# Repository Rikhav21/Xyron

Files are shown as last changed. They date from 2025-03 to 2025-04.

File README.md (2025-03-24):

# The 3d printer
This is just my CoreXY 3d printer that I want to print the frame for, and am trying to make the printer as cheap as possible.
The printer should end up being less than 150 dollars, but I also hope to make a filament extrusion system, and it also function as a laser cutter if needed. 
## CAD
This is the link for Onshape cad. https://cad.onshape.com/documents/d1304014e73009d6c11ef726/w/34172c7cf5d371a968e193e7/e/cf54ac2cfe94093a287dfb58
The CAD for this is in a step file, but does not have the belts, but they should go around the stepper botors, and attatach to the print head though the holes.

Design
## BOM
I tried to make it less than 150 dollars. http://docs.google.com/spreadsheets/d/1EGhT13h8WIjT6__bsCRffLh4skm1RX1gYrO3IXuM8uQ/edit?gid=0#gid=0

BOM

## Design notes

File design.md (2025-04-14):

made by @Rmardia \
Repositiory link: https://github.com/Rikhav21/Xyron \
Total hours so far: 74.5
- [x] I have a 3d printer right now.
## Day one
### Research
Today I spent a lot of time looking an=t a lot of different options and at the end I decided on making a core XY machine. I looked through a lot of different models on printables and I think I got the basic principles of how one of these machines would work.
### My goal
My goal with this 3d printer is to 3d print as many of the parts as possible from the frame, to whatever crosses my mind. I also feel like a auto print remover would be something simple to add with just a servo, that would make the printer way cooler.
### Design
I started with onshape, and got a liitle of the gantry done. 
### time
4 hours 30 minutes

IMounting 
## Day two
### Design
Today I learnt a little bit more about onShape and got continued with the assembaly. Most of my time just was spent figuring out how to use the assembaly.
### Time
5 hours and 30 minutes

gantry
## Day three
### Design
Today I continues working on the gantry and now have to work on the tool head. The X and Y linear rods are finished with the modeling.
### Time
6 hours.

gantry
## Day four
### Design
Today I did a lot of work on the gantry, and added some screws on the assembally, however I realized that I forgot about the idelers, so I have to do that later. 
### Time
Today I spent 5 hours on the design.
## Day five
### Design
Today I have redesign a lot of the parts because I forgot the idlers, I also redid the assembally and a ton of the parts, It was so annoying that I had to make so many changes for one tiny thing
Time 5 and a half hours.
## Day six
### Design
Today I did a lot of designing, made the x axis with the linear rods, and though about ways that I could do bed leveling. I decided on just using screws, and rubber bands to hold the bed in place
### Time
Six and a half hours.
## Day seven
### Design
Today I continued working on the bed and started my BOM.BOM. I finished most of it, then realized that I would also need am extruder, so I had to model a mount for that.
### Time
8 hours.
BOM
## Day Eight
### Design
Today I worked on the z axis movement and got some suggestions for the printer, so I also added some clearances. I updated my BOM, and got it down to $130 (Not counting filament, or taxes), and I realized that I forgot to mount my SKR Mini, so I will do that tomorrow.
https://docs.google.com/spreadsheets/d/1EGhT13h8WIjT6__bsCRffLh4skm1RX1gYrO3IXuM8uQ/edit?usp=drivesdk

### TIme
4 and a half hours.
## Day nine
### Design
Today I just adjusted some clearances, and mounted the board to the printer. I guess that Now I will submit the file, and ask for the grant, so I will keep my fingers crossed that it will get accepted.
Design
### Time
2 hours.

## Day nine
### Design
Today I mainly just ordered parts, and researched for some better deals. I also researched for a filament extruder.
### Time
Five and a half hours.

## Day ten
### Design
Today I satrted getting some of parts, and just did some assembling, and printed a hot end holder out of petg, although I did suffer some stringing, but it worked well enough.
### Time 
three hours.

## Day eleven
### Design
Today I just continued with assembly mounted the motors, and started screwing parts together. I might have made the holes too small for the heat set inserts, but at the end I expeanded it with a wood burner, so it worked out.
### Time
Seven hours.

## Day twelve
### Desgin
Today I worked on assembling the gantry, and I did a lot of trying to getting the bearings into the part where I could screw them into the back.
### Time
four and a half hours.

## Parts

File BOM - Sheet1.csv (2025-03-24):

Column 1 | Quantity | Cost | Amount | link | Column 3
Stepper Motors (3) | 1 | 25 | 25 | https://www.aliexpress.us/item/3256802068491329.html?mp=1
Extruder Stepper | 1 | 7 | 7 | https://www.aliexpress.us/item/3256805783540153.html?mp=1
BTT SKR MINI E3 Clone | 1 | 20 | 20 | https://www.aliexpress.us/item/3256806527609820.html?mp=1
Idlers | 3 | 0.53 | 4 | https://www.aliexpress.us/item/3256808316054525.html?mp=1
Linear rods (4) 8x300mm | 2 | 13.5 | 27 | https://www.aliexpress.us/item/3256803556267498.html?mp=1
LM8UU Linear Bearings (8) | 1 | 5.95 | 5.95 | https://www.aliexpress.us/item/3256808199237036.html?mp=1
End Stops | 1 | 2.17 | 2.17 | https://www.aliexpress.us/item/3256807318734333.html?mp=1
M3 16 mm bolts (100) | 1 | 3.89 | 3.89 | https://www.aliexpress.us/item/2251832608527529.html?mp=1
GT2 6mm 5m | 1 | 4.56 | 4.56 | https://www.aliexpress.us/item/2261800215268121.html?mp=1
PSU Transformer, 24 V , 100 W | 1 | 18.33 | 18.33 | https://www.aliexpress.us/item/3256807022510885.html?mp=1
Garolite for bed | 1 | 7.5 | 7.5 | https://www.aliexpress.us/item/3256807336994810.html?mp=1
MK8 clone | 1 | 6.98 | 6.98 | https://www.aliexpress.us/item/3256805028142213.html?mp=1
Part cooling fan | 1 | 1.19 | 1.19 | https://www.aliexpress.us/item/2251832639244297.html?mp=1
E3D V6 | 1 | 2.85 | 2.85 | https://www.aliexpress.us/item/3256806493734174.html?mp=1
F695 | 1 | 3.21 | 3.21 | https://www.aliexpress.us/item/3256808199237036.html?mp=1
M3 heatset inserts | 1 | 2.5 | 2.5 | https://www.aliexpress.us/item/3256807155790358.html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
 |  | total | 141 |  | Note: The total is after discounts and shipping, and taxes, so adding them all together, will not get the total.
Link to my CAD model : :https://cad.onshape.com/documents/d1304014e73009d6c11ef726/w/34172c7cf5d371a968e193e7/e/cf54ac2cfe94093a287dfb58

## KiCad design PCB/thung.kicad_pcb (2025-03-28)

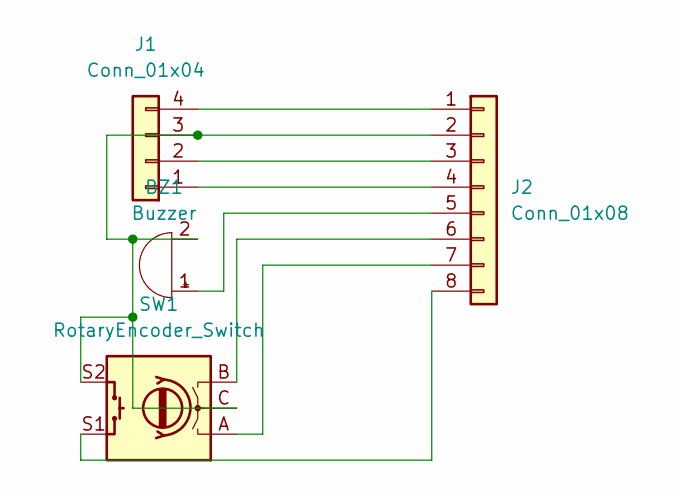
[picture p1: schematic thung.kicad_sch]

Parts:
BZ1: Buzzer; Buzzer_12x9.5RM7.6
J1: Conn_01x04; PinSocket_1x04_P2.54mm_Vertical
J2: Conn_01x08; PinSocket_1x08_P2.54mm_Vertical
SW1: RotaryEncoder_Switch; RotaryEncoder_Alps_EC11E-Switch_Vertical_H20mm

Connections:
unnamed: BZ1.1 (+), J2.5
unnamed: BZ1.2 (-), J1.3, J2.2, SW1.C, SW1.S2
unnamed: J1.1, J2.4
unnamed: J1.2, J2.3
unnamed: J1.4, J2.1
unnamed: J2.6, SW1.B
unnamed: J2.7, SW1.A
unnamed: J2.8, SW1.S1

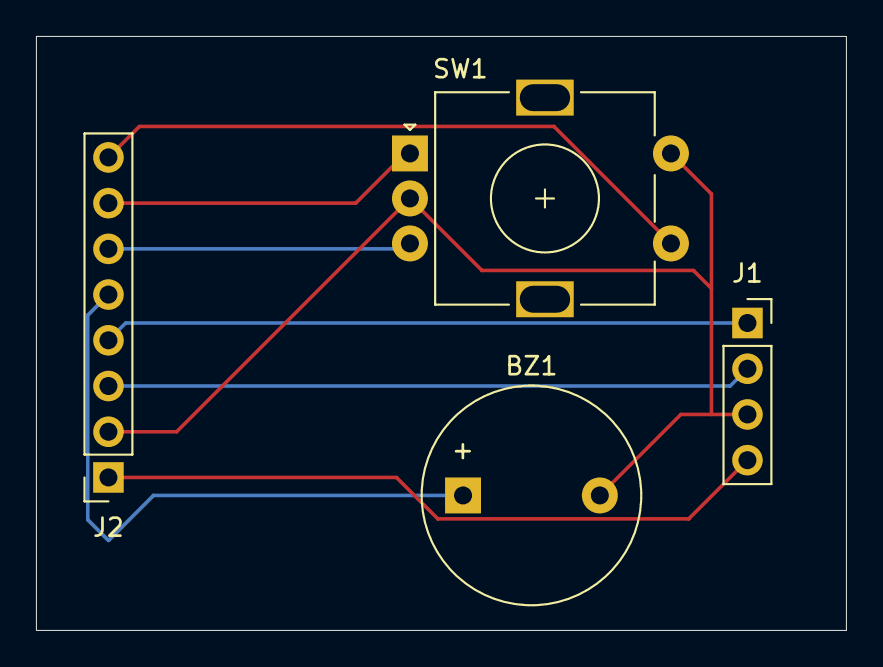
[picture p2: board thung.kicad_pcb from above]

Board: 2 copper layers, 45.0 x 33.0 mm, 4 parts (0 on the bottom side), 8 nets.

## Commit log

2025-03-28 Update and rename thung.kicad_pcb to PCB/thung.kicad_pcb
    [thung.kicad_pcb]
2025-03-28 Update and rename thung.kicad_sch to PCB/thung.kicad_sch
    [thung.kicad_sch]
